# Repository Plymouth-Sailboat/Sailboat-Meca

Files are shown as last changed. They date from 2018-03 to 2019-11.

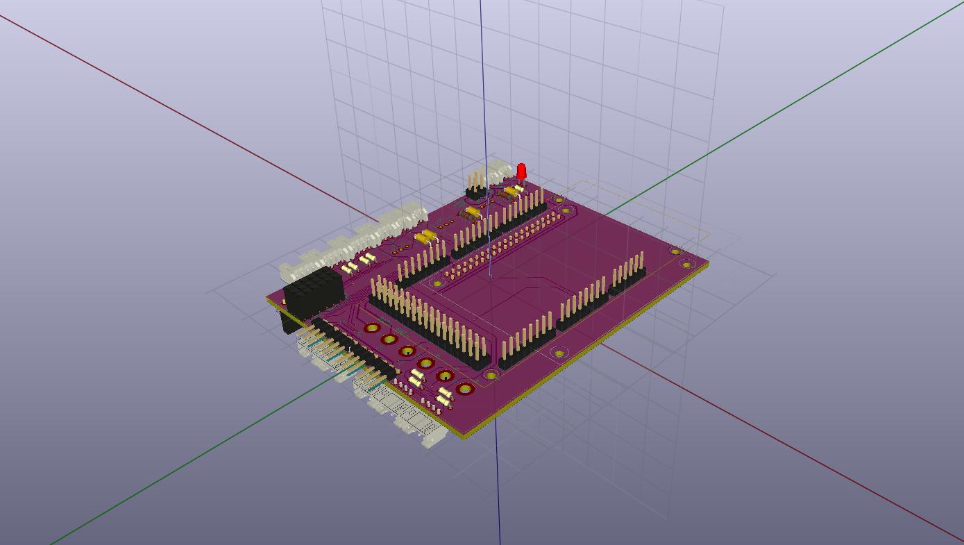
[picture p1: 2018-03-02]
Electronic Board/SailboatMainBoard.jpg

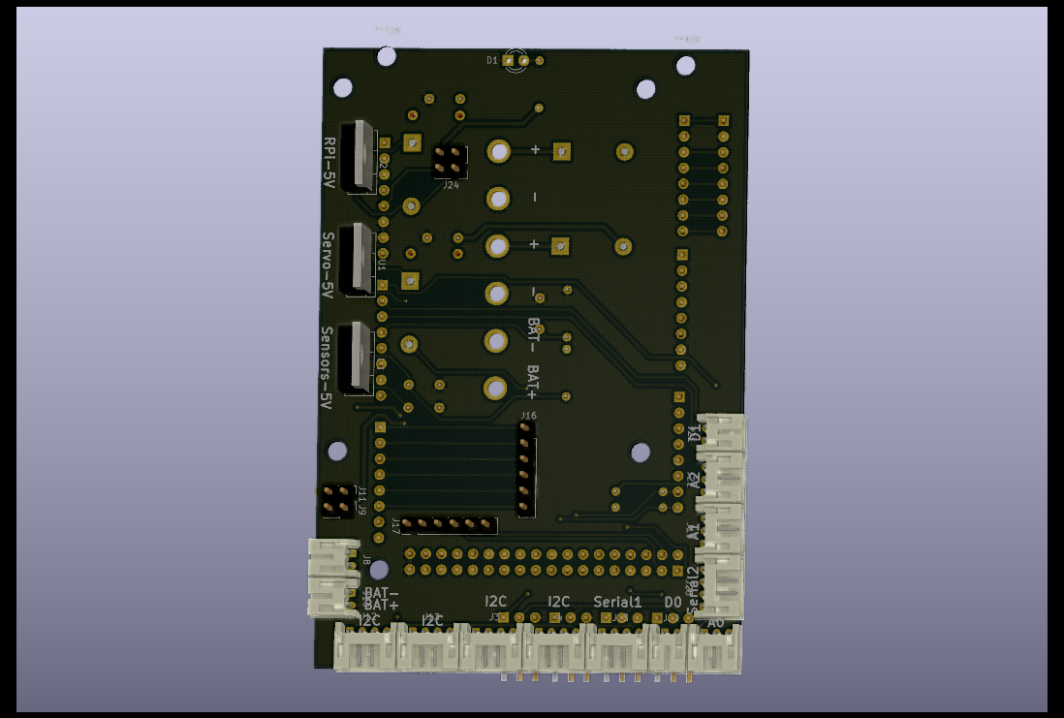
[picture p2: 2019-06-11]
Electronic Board/Sailboat Kicad/Board1-Arduino/3D/ArduinoIntBack.png

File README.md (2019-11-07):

# Sailboat-Meca

boatgif

This repository lists all the mechanical documents of the sailboat - Electronic Board and 3D Parts. It is used in conjunction with the [Arduino Repository](https://github.com/Plymouth-Sailboat/SailBoatArduinoInterface) and the [Raspberry Pi Repository](https://github.com/Plymouth-Sailboat/SailBoatROS).
This project was done by [Ulysse Vautier](https://ulyssevautier.github.io/) for his PhD in Autonomous Sailboat Navigation System at the University of Plymouth.

**A complete tutorial is available on the** [wiki](https://github.com/Plymouth-Sailboat/Sailboat-Meca/wiki).

The goal of such a project is to make an affordable, accessible and expandable control box to transform a RC sailboat into an autonomous Sailboat easily. The control box costs £86 to make.  
Once connected to the different sensors and actuators of the sailboat, it transforms it into an autonomous sailboat with already implemented navigation algorithms. Please see the [list of control algorithms](https://github.com/Plymouth-Sailboat/SailBoatROS/wiki/Controllers-List) already implemented.

Another option is to use off-the-shelf Shields to act as a connector interface for the Arduino. This is a cheaper alternative to the custom board, but removes the compactness of it. This is explained in the [wiki](https://github.com/Plymouth-Sailboat/Sailboat-Meca/wiki).

**For more information look at the Wikis. The project is separated into 3 categories : [SailboatMeca](https://github.com/Plymouth-Sailboat/Sailboat-Meca), [SailBoatROS](https://github.com/Plymouth-Sailboat/SailBoatROS) and [SailboatArduinoInterface](https://github.com/Plymouth-Sailboat/SailBoatArduinoInterface).**

**[SailboatMeca](https://github.com/Plymouth-Sailboat/Sailboat-Meca) explains the hardware configuration of the boat. The sensors that are used, how to build the control box and how to attach all the components to the control box.**

**[SailBoatROS](https://github.com/Plymouth-Sailboat/SailBoatROS) contains the code on the Raspberry Pi. It explains how to have a full environment ready on the Raspberry Pi 3B and Raspberry Pi 3B+ to have a working boat.**

**[SailBoatArduinoInterface](https://github.com/Plymouth-Sailboat/SailBoatArduinoInterface) explains how to upload the code to the Arduino. It also explains how to change the configuration files or how to add sensors to comply with your hardware configuration.  
Please look at all their wikis and READMEs.**

# Structure of this Repository

You fill find the 3D prints for waterproofing our sensors and the complete KiCad project for our Custom Circuit Board. The KiCad projects come with 3D models of the boards and the Gerber files needed to manufacture them.

# Off-The-Shelf System

Assembled System

This is a new hardware architecture using mostly commercial modules for Arduino and Raspberry Pi, using [SeeedStudio grove shields](http://wiki.seeedstudio.com/Grove_System/). This version is a bit bigger but a cheaper and more easily attainable than manufactured custom boards.  
All the previous components used are still compatible, only connectors need to be changed. Also the battery used are Li-ion battery packs now. Everything is explained in the [wiki](https://github.com/Plymouth-Sailboat/Sailboat-Meca/wiki).

# Custom Circuit Board

Arduino Interface Board

Our custom board is composed of two boards, stacking with each others. One stacking with the Arduino Mega and another one stacking with the Raspberry Pi.
These custom boards manages power, connection to sensors and motors and communications between Raspberry Pi, the Arduino and all the peripheral devices.

## Arduino Interface Board

The Arduino Interface Board exports the Arduino's connector to interface them with strong, more robust JST connectors. This board also manages the power to all of the peripheral devices. You can find the complete KiCad Project, Gerber files and 3Ds of the boards at [Arduino Interface Board Folder](/Electronic%20Board/Sailboat%20Kicad/Board1-Arduino).  
This board stacks with the Arduio Mega and the Raspberry Pi Interface Board below.

## Raspberry Pi Interface Board

The Raspberry Pi Board is only a board to level all the components to make the overall structure compact. It connects the power to the Raspberry Pi and interface the Radio Receiver to the Arduino. You can find the complete KiCad Project, Gerber files and 3Ds of the boards at [Raspberry Pi Interface Board Folder](/Electronic%20Board/Sailboat%20Kicad/Board2-RPI).   
This board stacks with the Arduino Interface Board and the Raspberry Pi.

# Bill Of Material

The bill of material is available [here](BOM.xlsx). It details all the mechanical and electrical components with the sensors and motors for our boats. It also gives all the link to suppliers to buy the components we use. We mainly purchase our components from [RS](https://uk.rs-online.com/web/) and we use a third-party manufacturer to make the boards [SeeedStudio](https://www.seeedstudio.com/fusion_pcb.html).

The overall price of a whole autonomous sailboat comes to £605.65 (considering the IMU used is 1/3 of the price). The custom board itself costs £86 overall - with third-party service to print the boards.

# Installation

## Requirements

* Raspberry Pi 3 Model B with [ROS and our package](https://github.com/Plymouth-Sailboat/SailBoatROS)
* Arduino Mega with [our code](https://github.com/Plymouth-Sailboat/SailBoatArduinoInterface)
* Custom Boards above

All the installation for each of these devices are explained in their respective Repository.

To get your custom board printed via SeeedStudio, we suggest following the tutorial in the [wiki](https://github.com/Plymouth-Sailboat/Sailboat-Meca/wiki)

Once the boards are soldered all you need is to stack them with the Arduino and Raspberry Pi. Connect your Raspberry Pi to the Arduino via USB and your Control Box is ready to host a new sailboat.

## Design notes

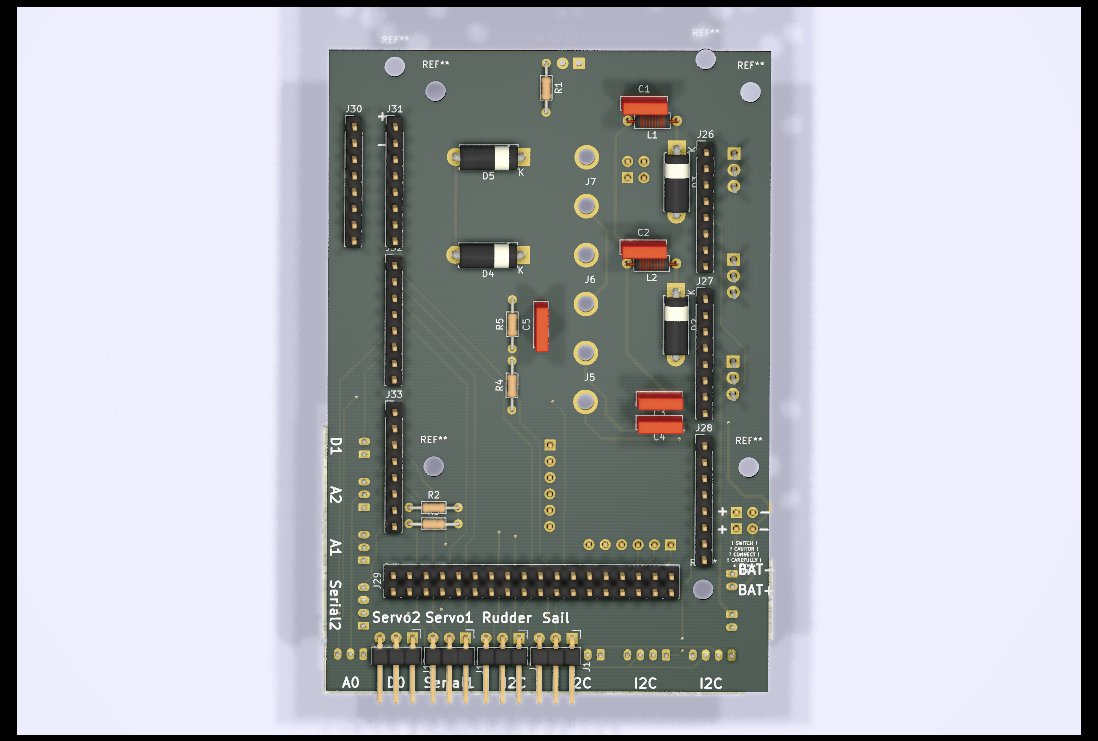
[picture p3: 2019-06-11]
Electronic Board/Sailboat Kicad/Board1-Arduino/3D/ArduinoIntFront.png

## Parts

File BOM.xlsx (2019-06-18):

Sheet: BOM
Name | Description | Price | Source
Boat | Rubix
PCB Boards |  | £80.51 | Card Component'!A1
SeeedStudio | PCB Manufacturing x 2 | £6.00 | https://www.seeedstudio.com/fusion_pcb.html
Mechanical Parts |  | £32.82 | Mechanical Parts'!A1
Sensors |  | £434.36 | Sensors!A1
Battery | 2S 4000mAh | £12.44 | https://hobbyking.com/en_us/turnigy-4000mah-2s-30c-hardcase-pack-roar-approved-de-warehouse.html
Raspberry Pi 3 B |  | £32.00 | https://thepihut.com/products/raspberry-pi-3-model-b
Arduino Mega |  | £7.53 | https://hobbyking.com/en_us/mega-2560-r3-atmega2560-16au-board-plus-usb-cable-1.html
 |  | £605.65 | Note that most of the cost comes from the sensors. Cheaper alternatives can be found for the sensors and it will still be compatible with the whole system.

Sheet: Card Component
Name | Value | Quantity | Reference | Description | Price exc VAT | Price | Total | Source | VAT | 1.2
Capacitor | 0.33uF | 1 | C320C334M5U5TA |  | £0.11 | 0.1332 | £0.11 | https://uk.rs-online.com/web/p/ceramic-multilayer-capacitors/8015390/
Capacitor | 0.1uF | 1 | C315C104M5U5TA |  | £0.08 | 0.0912 | £0.08 | https://uk.rs-online.com/web/p/ceramic-multilayer-capacitors/5381203/
Capacitor | 4.7uF | 2 | C320C475K3N5TA91707301 |  | £0.29 | 0.3504 | £0.58 | https://uk.rs-online.com/web/p/ceramic-multilayer-capacitors/1365581/
Inductor | 3.3uH | 2 | B78108S1332K000 |  | £0.29 | 0.3468 | £0.58 | https://uk.rs-online.com/web/p/leaded-inductors/1910431/
JST-PH-S2B Angled |  | 3 | S2B-PH-K-S |  | £0.38 | 0.456 | £1.14 | https://uk.rs-online.com/web/p/pcb-headers/8201494
JST-PH-S3B Angled |  | 3 | S3B-PH-K-S |  | £0.38 | 0.456 | £1.14 | https://uk.rs-online.com/web/p/pcb-headers/8201504
JST-PH-S4B Angled |  | 2 | S4B-PH-K-S |  | £0.38 | £0.46 | £0.76 | https://uk.rs-online.com/web/p/pcb-headers/8201507/
LED | G | 1 |  |  |  | £0.00 | £0.00
Pin Header 1x2 |  | 2 | 251-8086 |  | £0.08 | £0.10 | £0.16 | https://uk.rs-online.com/web/p/pcb-headers/2518086/
Pin Header 1x3 Angled |  | 3 | 90121-0763 |  | £0.43 | £0.52 | £1.30 | https://uk.rs-online.com/web/p/pcb-headers/3606437/
Pin Header 1x6 |  | 2 | 68000-406HLF |  | £0.20 | £0.24 | £0.40 | https://uk.rs-online.com/web/p/pcb-headers/6812994/
Pin Header 1x8 |  | 6 | M20-9990846 |  | £0.20 | £0.24 | £1.20 | https://uk.rs-online.com/web/p/pcb-headers/6812991/
Pin Header 2x18 |  | 0 | 90131-0138 |  | £0.84 | £1.01 | £0.00 | https://uk.rs-online.com/web/p/pcb-headers/6703487/
Pin Header 2x2 |  | 1 | 826632-2 |  | £0.28 | £0.33 | £0.28 | https://uk.rs-online.com/web/p/pcb-headers/6695288/
Regulator | L7805 | 1 | L7805CV | 5V 1.5A | £0.59 | £0.71 | £0.59 | https://uk.rs-online.com/web/p/linear-voltage-regulators/7931346/
Regulator | R-78B5.0-2.0 | 2 | R-78B5.0-2.0 | 5V 2A | £7.94 | £9.53 | £15.88 | https://uk.rs-online.com/web/p/switching-regulators/1392959/
Resistor | 330 | 1 | LR1F330R |  | £0.05 | £0.06 | £0.05 | https://uk.rs-online.com/web/p/through-hole-fixed-resistors/0148382/
Resistor | 4k7 | 2 | 707-7726 |  | £0.10 | £0.12 | £0.20 | https://uk.rs-online.com/web/p/through-hole-fixed-resistors/7077726/
Socket Header 1x3 |  | 7 | 251-8187 |  | £0.32 | £0.38 | £2.22 | https://uk.rs-online.com/web/p/pcb-sockets/2518187/
Socket Header 1x6 |  | 2 | 4320-01074-0 |  | £0.94 | £1.12 | £1.87 | https://uk.rs-online.com/web/p/pcb-sockets/1613692/
Socket Header 1x8 |  | 1 | 215297-8 |  | £0.69 | £0.83 | £0.69 | https://uk.rs-online.com/web/p/pcb-sockets/4958587/
Socket Header 2x2 |  | 1 | 803-87-004-10-001101 |  | £0.45 | £0.54 | £0.45 | https://uk.rs-online.com/web/p/pcb-sockets/7022934/
Socket Header 2x20 |  | 1 | A-BL254-DG-G40D |  | £1.78 | £2.13 | £1.78 | https://uk.rs-online.com/web/p/pcb-sockets/6742369/
Schottky Diode |  | 4 | SR560 |  | £0.07 | £0.09 | £0.30 | https://uk.rs-online.com/web/p/rectifier-schottky-diodes/9179120/
Resistor | 20k | 1 | LR1F20K |  | £0.04 | £0.05 | £0.04 | https://uk.rs-online.com/web/p/through-hole-fixed-resistors/1251166/
Resistor | 12k | 1 | MRS25000C1202FCT00 |  | £0.08 | £0.09 | £0.08 | https://uk.rs-online.com/web/p/through-hole-fixed-resistors/6832989/
RMG Switch |  | 1 |  |  | £34.50 | £41.40 | £34.50 | https://www.rmgsailwinch.com.au/rmg/products/RMGSwitch%252dStd.html
HXT 4 Prebuilt |  | 1 |  |  | £0.72 | £0.86 | £0.72 | https://hobbyking.com/en_us/hxt-4mm-gold-connector-w-pre-installed-bullets-10pcs-set.html
 |  |  |  |  |  |  | £67.09
 |  |  |  |  |  |  | £80.51

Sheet: Mechanical Parts
Name | Value | Quantity | Reference | Description | Price exc VAT | Price | Total | Source | VAT | 1.2
RMG Sailwinch |  | 1 |  | Excluded in total | £206.60 | £247.92 | £206.60 | https://www.rmgsailwinch.com.au/rmg/products/380ES.html
KingMax Servo |  | 1 |  |  | £24.99 | £29.99 | £24.99 | https://www.componentshop.co.uk/61g-digital-sail-winch-servo-6-turn-programmable.html
Threaded Inserts M3 |  | 20 |  |  | £0.10 | £0.12 | £1.92 | https://uk.rs-online.com/web/p/inserts/0278534/
Spacers | 10mm | 10 | R30-3001002 |  | £0.01 | £0.01 | £0.07 | https://uk.rs-online.com/web/p/threaded-hex-spacers/1256002/
HXT4mm Cable |  | 1 |  |  | £0.76 | £0.92 | £0.76 | https://hobbyking.com/en_us/hxt4mm-w-12awg-silicon-wire-10cm-esc-side-5pcs-bag.html
Flex Ribbon Rpi | 300mm | 1 |  |  | £2.00 | £2.40 | £2.00 | https://thepihut.com/products/adafruit-flex-cable-for-raspberry-pi-camera-300mm-12
Velcro | 1m | 1 |  |  | £3.07 | £3.68 | £3.07 | https://hobbyking.com/en_us/polyester-velcro-peel-n-stick-self-adhesive-v-strong-1mtr.html
 |  |  |  |  |  | £0.00 | £0.00
 |  |  |  |  |  |  | £32.82
 |  |  |  |  |  |  | £39.38
 |  |  |  |  |  | Big Boat | £214.43

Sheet: Sensors
Name | Value | Quantity | Reference | Description | Price exc VAT | Price | Total | Source | VAT | 1.2
Xsens |  | 1 | Mti-3-8A7G6-DK | AHRS+Compass | £262.78 | £315.34 | £262.78 | https://shop.xsens.com/shop/mti-1-series/mti-1-series-dk/mti-3-8a7g6-dk
GPS Module |  | 1 |  |  | £5.08 | £6.10 | £5.08 | https://www.banggood.com/GPS-Module-with-Ceramic-Antenna-GPS-Receiver-TTL9600-Ublox-Module-for-Multirotor-p-1100984.html
Radio Transmitter + Receiver 6CH |  | 1 | T6A |  | £14.27 | £17.12 | £14.27 | https://hobbyking.com/en_us/hobby-king-2-4ghz-6ch-tx-rx-v2-mode-1.html
Wind Sensor |  | 1 | e-vane |  | £91.50 | £109.80 | £91.50 | https://www.inspeed.com/wind_speed_direction/Vane.asp
Raspberry Pi Camera |  | 1 |  |  | £24.50 | £29.40 | £24.50 | https://www.modmypi.com/pis-and-peripherals-1139/raspberry-pi-camera-board-v2-8mp1080p
AIS Receiver |  | 1 | B01GDN1T4S |  | £28.98 | £34.78 | £28.98 | https://www.amazon.co.uk/NooElec-NESDR-SMArt-Enclosure-R820T2-Based/dp/B01GDN1T4S
JST PHR-2 |  | 3 | PHR-2 |  | £0.03 | £0.04 | £0.09 | https://uk.rs-online.com/web/p/pcb-connector-housings/8201466/
JST PHR-3 |  | 2 | PHR-3 |  | £0.04 | £0.04 | £0.07 | https://uk.rs-online.com/web/p/pcb-connector-housings/8201475/
JST PHR-4 |  | 2 | PHR-4 |  | £0.04 | £0.05 | £0.08 | https://uk.rs-online.com/web/p/pcb-connector-housings/8201478/
JST Cable |  | 15 | SPH-26L-300 |  | £0.47 | £0.56 | £7.01 | https://uk.rs-online.com/web/p/products/8201412/
 |  |  |  |  |  | £0.00 | £0.00
 |  |  |  |  |  |  | £434.36
 |  |  |  |  |  |  | £521.23

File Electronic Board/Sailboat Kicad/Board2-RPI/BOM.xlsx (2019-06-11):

Id | Designator | Package | Quantity | Designation | Supplier and ref
1 | J29,J25,J26,J27,J28,J30,J4 | Socket_Strip_Straight_1x03_Pitch2.54mm | 7 | Conn_01x03_Female
2 | J33 | Socket_Strip_Straight_1x08_Pitch2.54mm | 1 | Conn_01x08_Female
3 | J23,J5 | Pin_Header_Straight_2x20_Pitch2.54mm | 2 | Conn_02x20_Odd_Even
4 | J1,J2 | Socket_Strip_Straight_1x06_Pitch2.54mm | 2 | Conn_01x06
5 | J3 | Socket_Strip_Straight_2x02_Pitch2.54mm | 1 | Conn_02x02_Odd_Even
6 | REF**,REF**,REF**,REF**,REF**,REF** | MountingHole_3.2mm_M3 | 6 | MountingHole_3.2mm_M3

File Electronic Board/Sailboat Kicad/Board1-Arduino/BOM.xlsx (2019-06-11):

Id | Designator | Package | Quantity | Designation | Supplier and ref
1 | J20,J8,J10,J21 | JST_PH_S2B-PH-K_1x02_P2.00mm_Horizontal | 4 | Conn_01x02_Male
2 | D1 | LED_D3.0mm | 1 | G
3 | REF**,REF**,REF**,REF**,REF**,REF**,REF** | MountingHole_3.2mm_M3 | 7 | MountingHole_3.2mm_M3
4 | J28,J30,J32,J27,J31,J33,J26 | PinHeader_1x08_P2.54mm_Vertical | 7 | Conn_01x08_Male
5 | J29 | PinHeader_2x18_P2.54mm_Vertical | 1 | Conn_02x18_Odd_Even
6 | J4,J3,J13,J23,J25,J12 | JST_PH_S4B-PH-K_1x04_P2.00mm_Horizontal | 6 | Conn_01x04_Male
7 | J5,J7,J6 | BAT-CONN | 3 | Conn_01x02_Female
8 | J18,J19,J22 | JST_PH_S3B-PH-K_1x03_P2.00mm_Horizontal | 3 | Conn_01x03_Male
9 | J1,J15,J14,J2 | PinHeader_1x03_P2.54mm_Horizontal | 4 | Conn_01x03_Male
10 | J11,J9 | PinHeader_1x02_P2.54mm_Vertical | 2 | Conn_01x02_Male
11 | J24 | PinHeader_2x02_P2.54mm_Vertical | 1 | Conn_02x02_Odd_Even
12 | J16,J17 | PinHeader_1x06_P2.54mm_Vertical | 2 | Conn_01x06_Male
13 | R5 | R_Axial_DIN0204_L3.6mm_D1.6mm_P7.62mm_Horizontal | 1 | 12k
14 | R2,R3 | R_Axial_DIN0204_L3.6mm_D1.6mm_P7.62mm_Horizontal | 2 | 4k7
15 | R4 | R_Axial_DIN0204_L3.6mm_D1.6mm_P7.62mm_Horizontal | 1 | 20k
16 | U3,U1,U2 | TO-220-3_Vertical | 3 | L7805
17 | L1,L2 | L_Axial_L5.3mm_D2.2mm_P7.62mm_Horizontal_Vishay_IM-1 | 2 | 3.3uH
18 | C1,C2 | C_Rect_L7.0mm_W2.0mm_P5.00mm | 2 | 4.7uF
19 | R1 | R_Axial_DIN0204_L3.6mm_D1.6mm_P7.62mm_Horizontal | 1 | 330
20 | D4,D5,D2,D3 | D_5W_P10.16mm_Horizontal | 4 | D_Schottky
21 | C3 | C_Rect_L7.0mm_W2.0mm_P5.00mm | 1 | 0.33uF
22 | C4 | C_Rect_L7.0mm_W2.0mm_P5.00mm | 1 | 0.1uF
23 | C5 | C_Rect_L7.0mm_W2.0mm_P5.00mm | 1 | 1uF

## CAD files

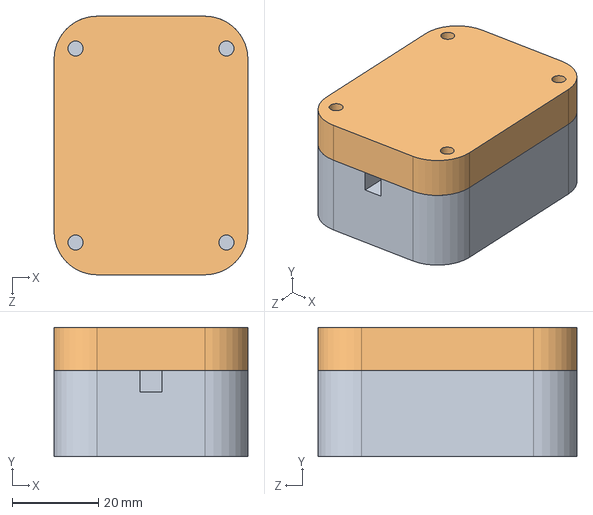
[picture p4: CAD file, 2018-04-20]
3D Prints/Adafruit Ultimate GPS Box/GPS.SLDASM
45.0 x 30.0 x 60.0 mm
GPSBot
GPSTop

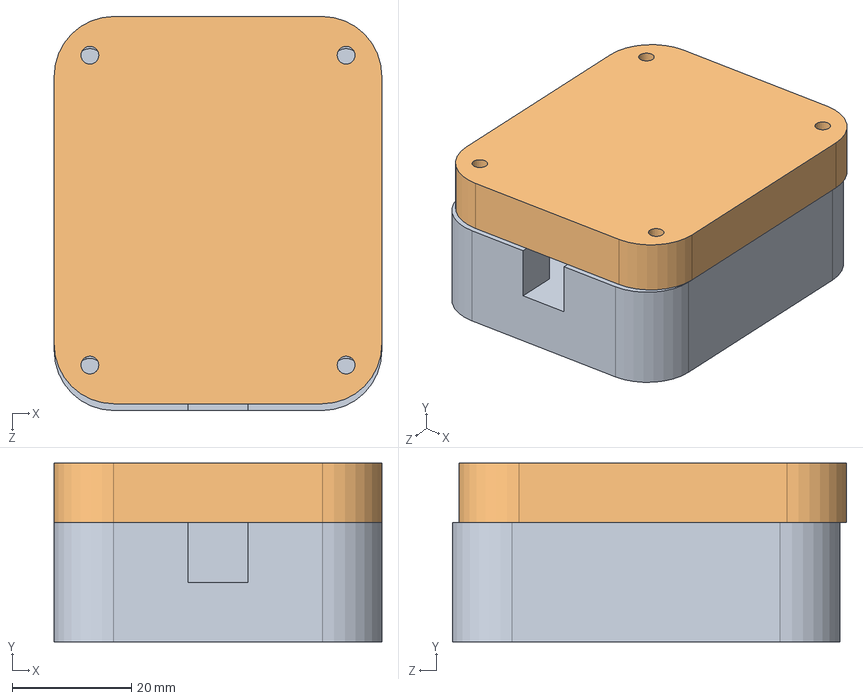
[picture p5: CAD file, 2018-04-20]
3D Prints/XSens Box/Xsens.SLDASM
55.0 x 30.0 x 66.1 mm
XSensBot
XSensTop

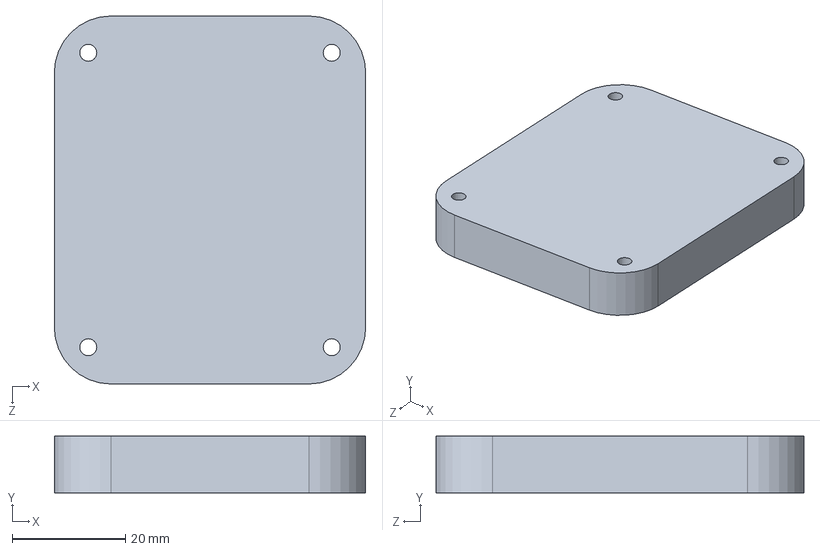
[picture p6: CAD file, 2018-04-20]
3D Prints/XSens Box/XSensTop.SLDPRT
55.0 x 10.0 x 65.0 mm

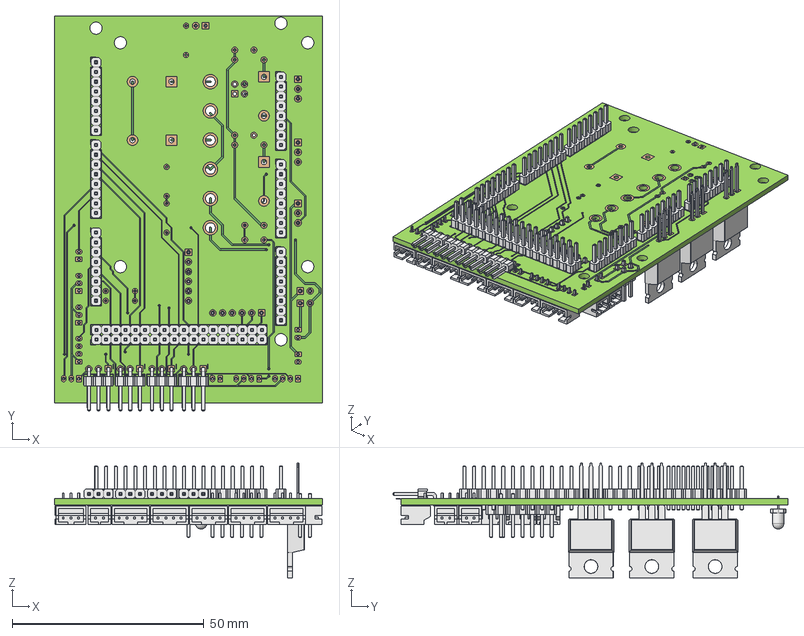
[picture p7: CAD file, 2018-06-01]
Electronic Board/Sailboat Kicad/Board1-Arduino/3D/ArduinoInt.FCStd
70.0 x 103.1 x 30.0 mm
Board
D1
J11
J12
J13
J14
J15
J16
J17
J18
J19
J20
J21
J22
J24
J31
J32
J3
J4
J5
J6
J7
J8
U1
U2
U3
J34
J35
J36
J37
J2
J23
J25
F_Cu_0
bPad_107
tPad_108
B_Cu_31
B_SilkS_36
F_SilkS_37

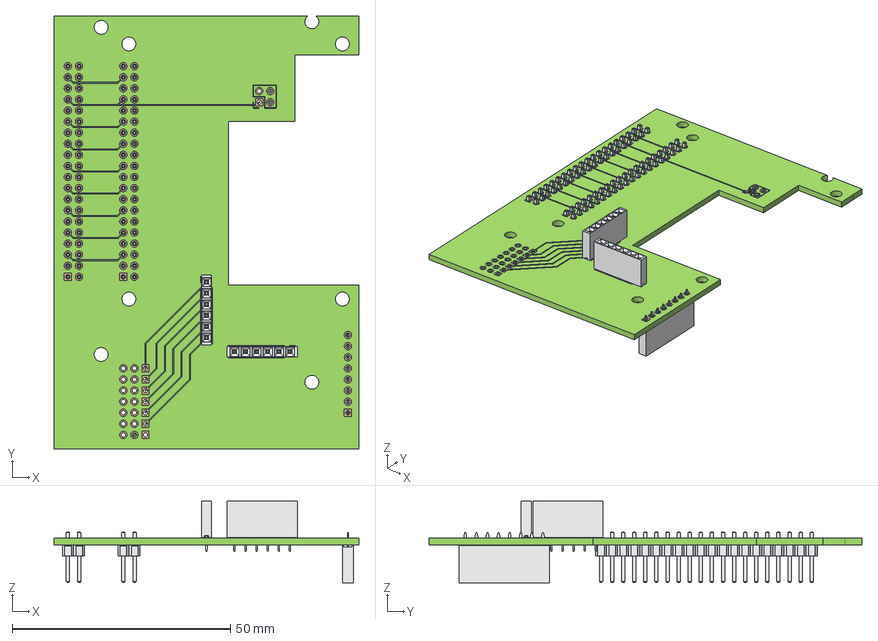
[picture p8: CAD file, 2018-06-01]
Electronic Board/Sailboat Kicad/Board2-RPI/3D/RPiInt.FCStd
69.9 x 99.1 x 18.7 mm
Board
J33
J23
J1
J2
J5
F_Cu_0
bPad_107
tPad_108
B_Cu_31
B_SilkS_36
F_SilkS_37

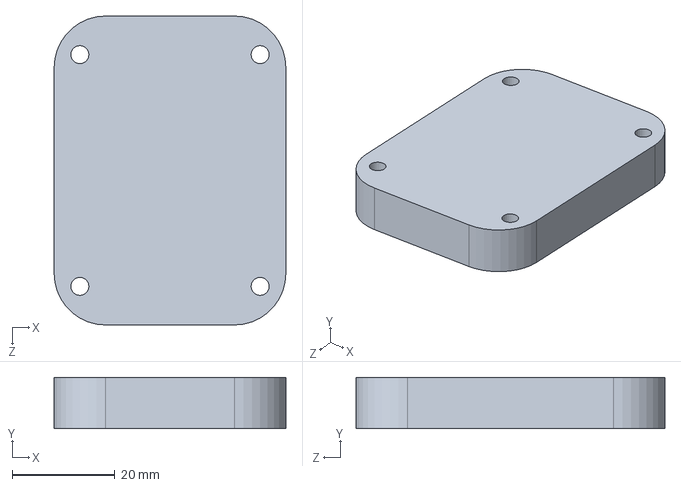
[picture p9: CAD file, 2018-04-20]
3D Prints/Adafruit Ultimate GPS Box/GPSTop.SLDPRT
45.0 x 10.0 x 60.0 mm

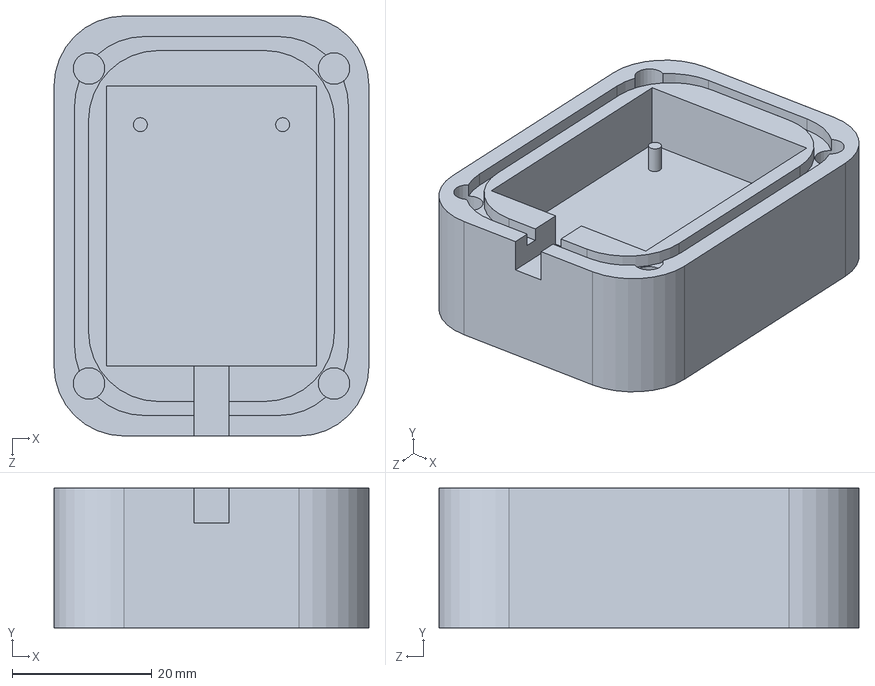
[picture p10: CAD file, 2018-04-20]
3D Prints/Adafruit Ultimate GPS Box/GPSBot.SLDPRT
45.0 x 20.0 x 60.0 mm

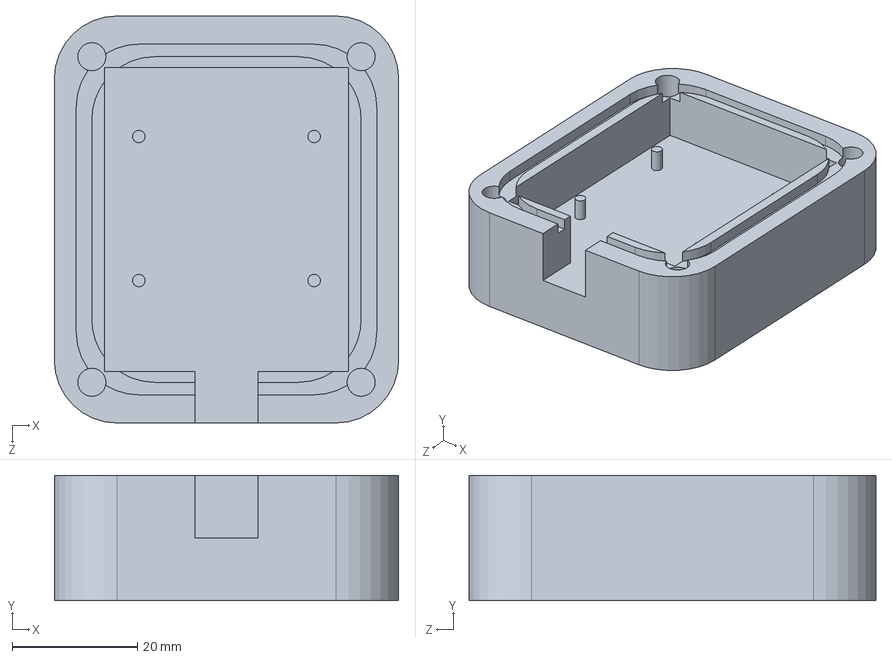
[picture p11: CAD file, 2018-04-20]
3D Prints/XSens Box/XSensBot.SLDPRT
55.0 x 20.0 x 65.0 mm

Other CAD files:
3D Prints/Adafruit Ultimate GPS Box/GPSBot.STL
3D Prints/Adafruit Ultimate GPS Box/GPSTop.STL
3D Prints/XSens Box/XSensBot.STL
3D Prints/XSens Box/XSensTop.STL
Electronic Board/Sailboat Kicad/Board2-RPI/3D/RPiInt.stl

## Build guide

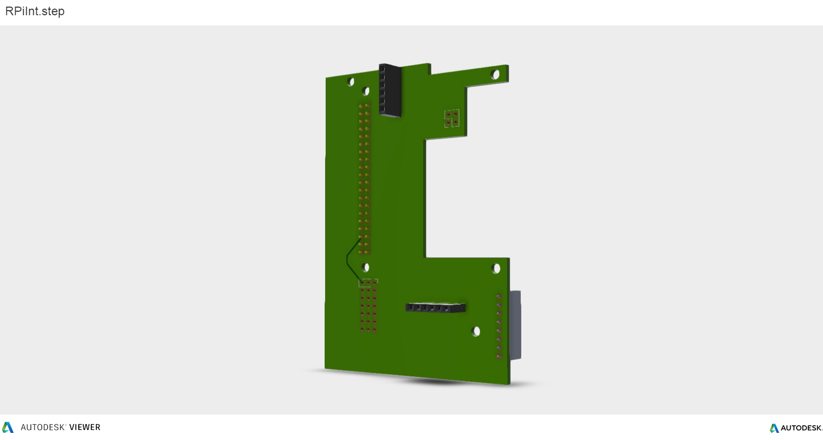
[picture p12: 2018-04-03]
Electronic Board/Sailboat Kicad/Board2-RPI/3D/RPiInt.step.png

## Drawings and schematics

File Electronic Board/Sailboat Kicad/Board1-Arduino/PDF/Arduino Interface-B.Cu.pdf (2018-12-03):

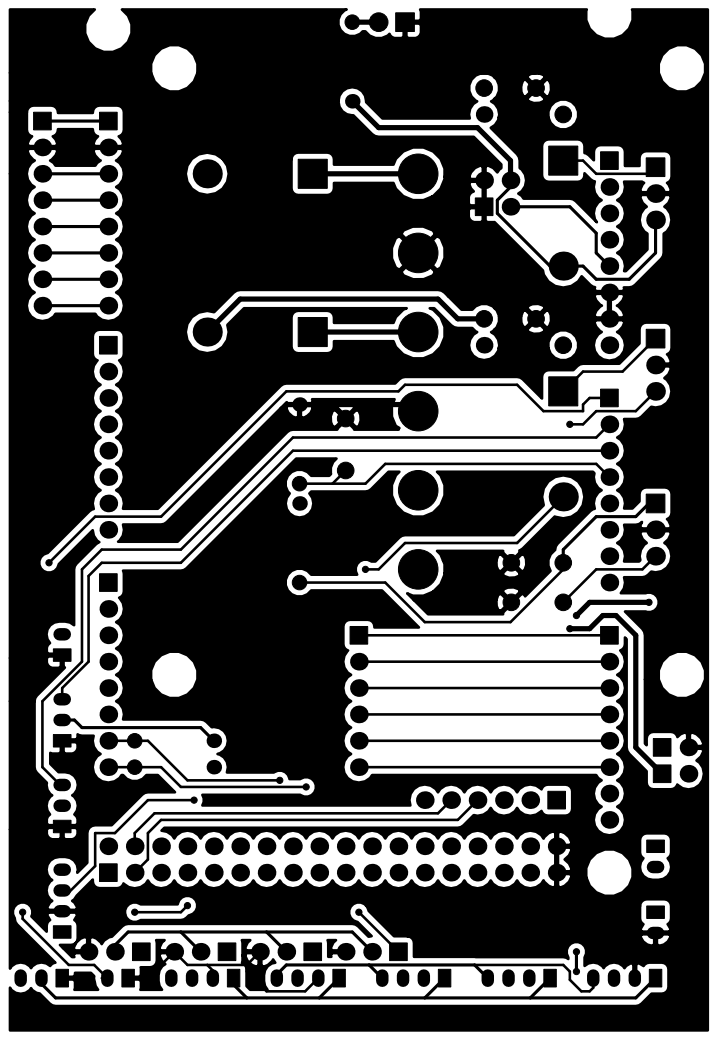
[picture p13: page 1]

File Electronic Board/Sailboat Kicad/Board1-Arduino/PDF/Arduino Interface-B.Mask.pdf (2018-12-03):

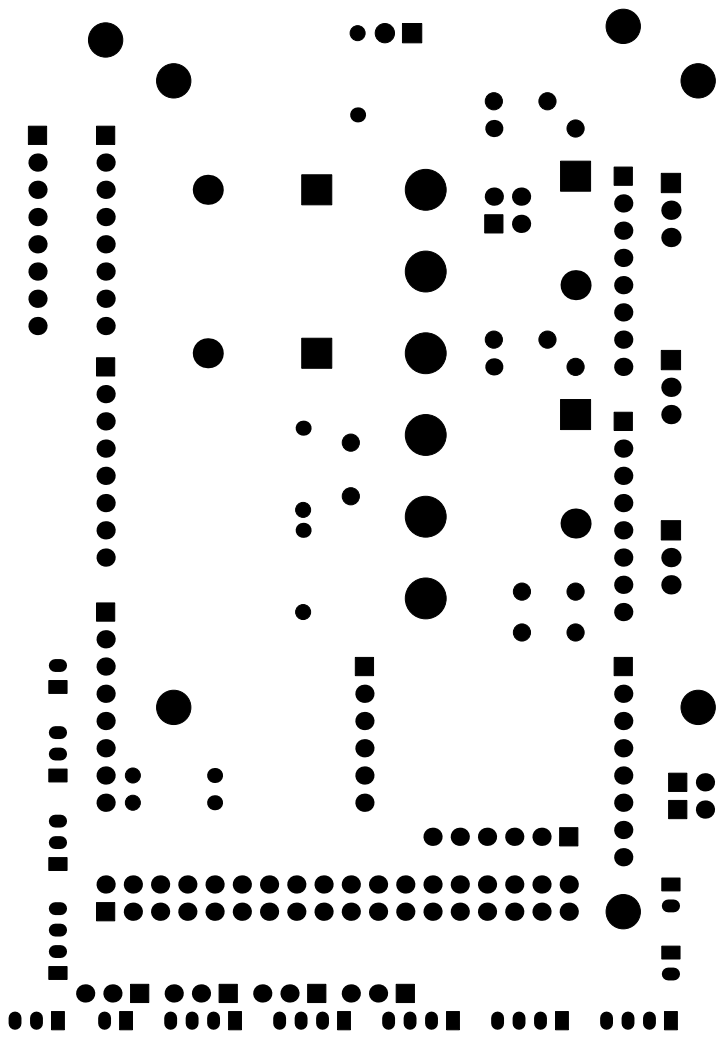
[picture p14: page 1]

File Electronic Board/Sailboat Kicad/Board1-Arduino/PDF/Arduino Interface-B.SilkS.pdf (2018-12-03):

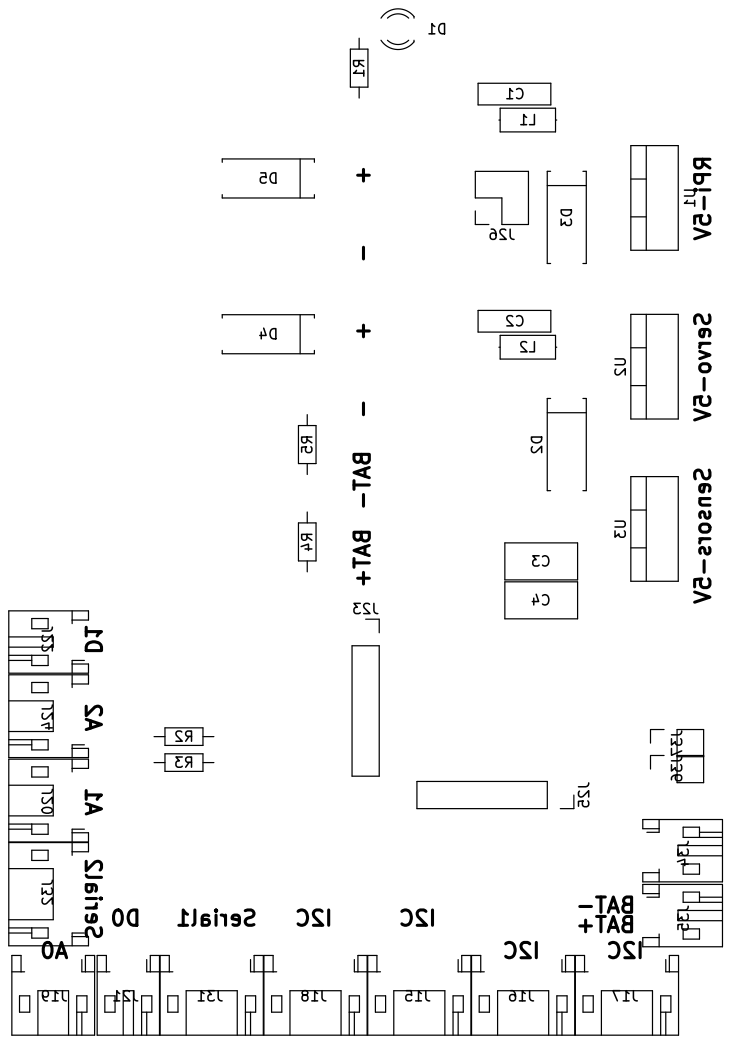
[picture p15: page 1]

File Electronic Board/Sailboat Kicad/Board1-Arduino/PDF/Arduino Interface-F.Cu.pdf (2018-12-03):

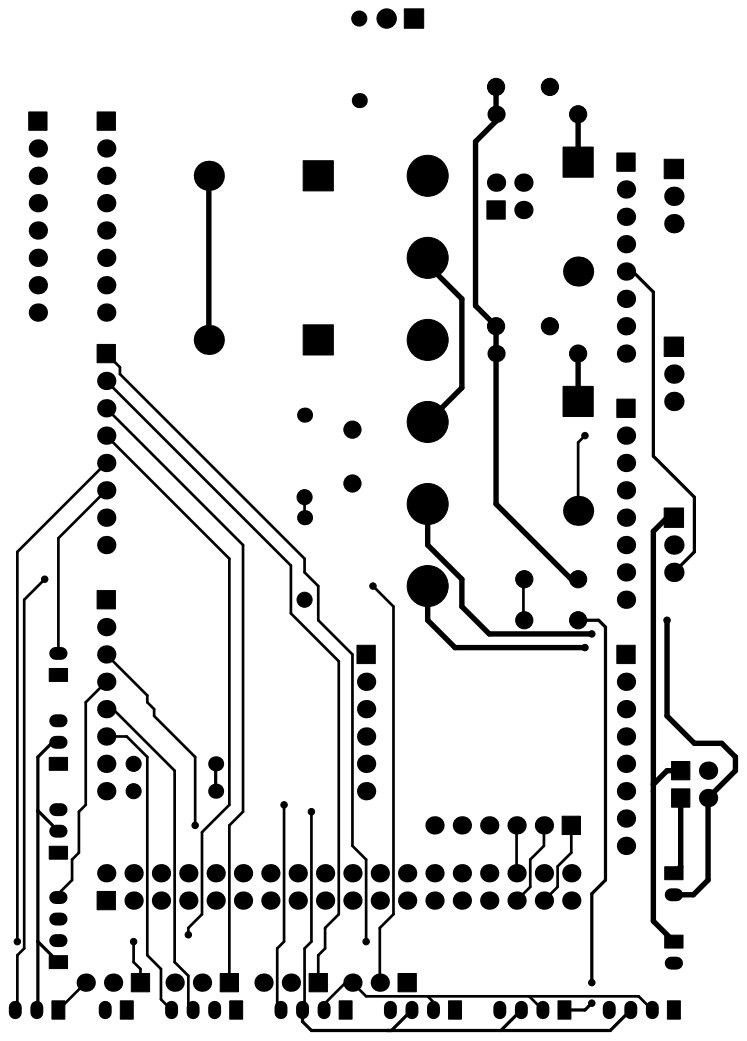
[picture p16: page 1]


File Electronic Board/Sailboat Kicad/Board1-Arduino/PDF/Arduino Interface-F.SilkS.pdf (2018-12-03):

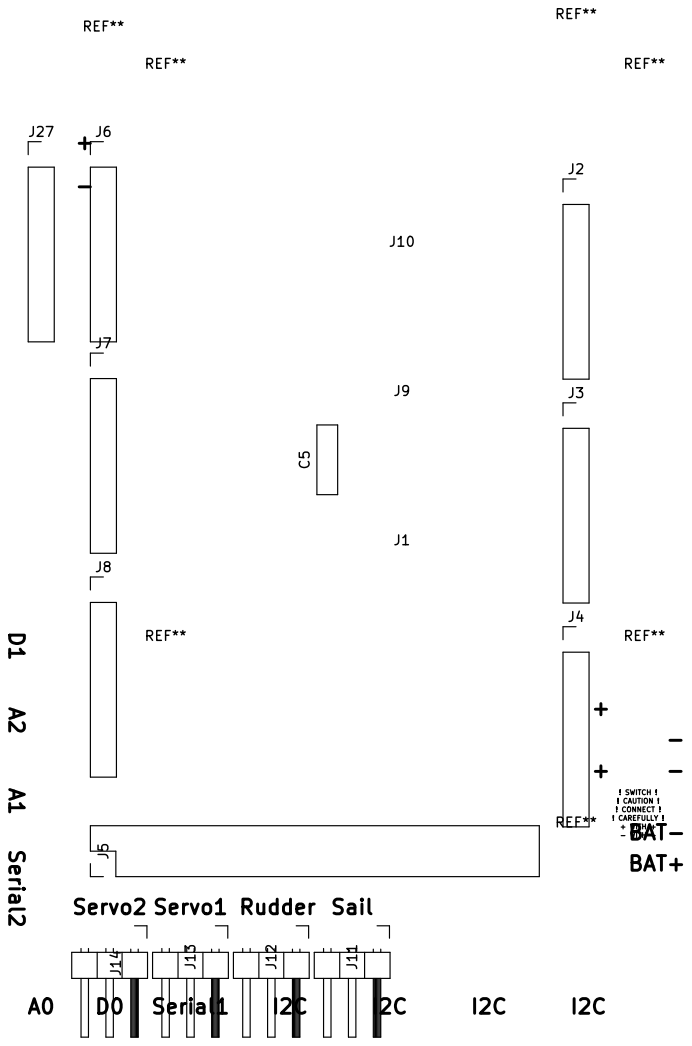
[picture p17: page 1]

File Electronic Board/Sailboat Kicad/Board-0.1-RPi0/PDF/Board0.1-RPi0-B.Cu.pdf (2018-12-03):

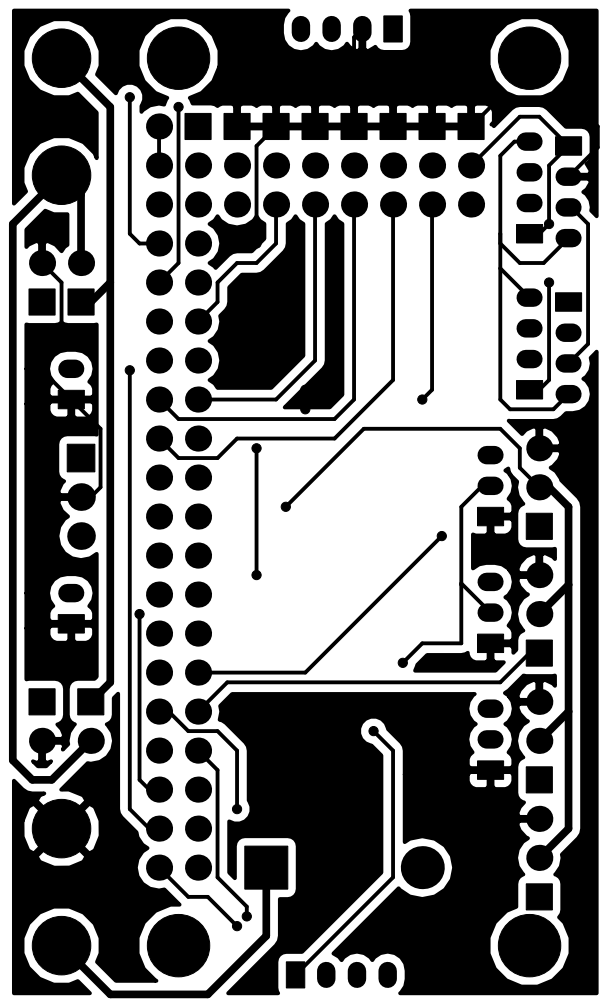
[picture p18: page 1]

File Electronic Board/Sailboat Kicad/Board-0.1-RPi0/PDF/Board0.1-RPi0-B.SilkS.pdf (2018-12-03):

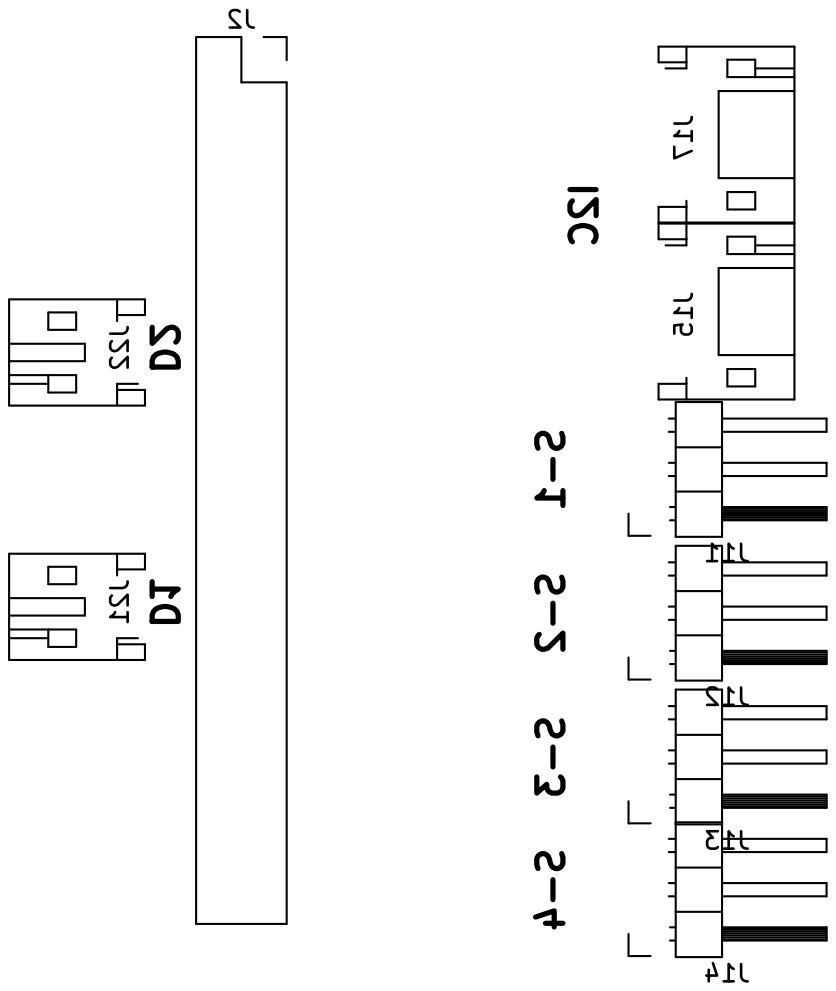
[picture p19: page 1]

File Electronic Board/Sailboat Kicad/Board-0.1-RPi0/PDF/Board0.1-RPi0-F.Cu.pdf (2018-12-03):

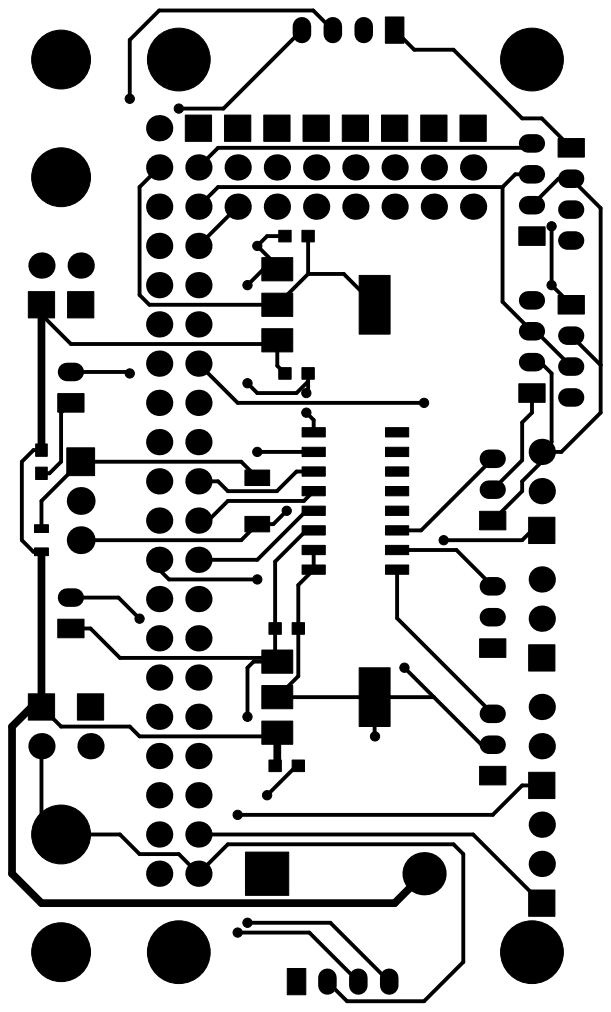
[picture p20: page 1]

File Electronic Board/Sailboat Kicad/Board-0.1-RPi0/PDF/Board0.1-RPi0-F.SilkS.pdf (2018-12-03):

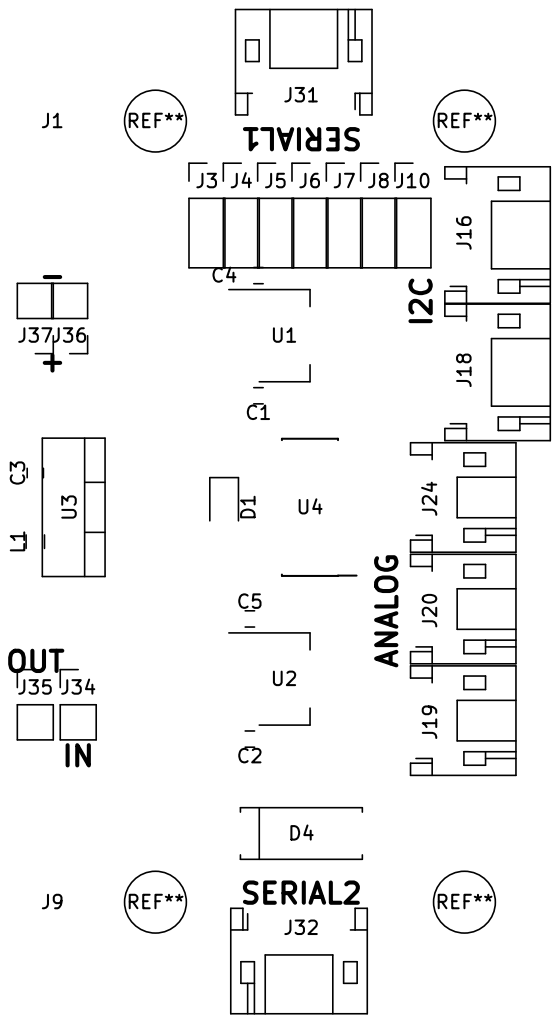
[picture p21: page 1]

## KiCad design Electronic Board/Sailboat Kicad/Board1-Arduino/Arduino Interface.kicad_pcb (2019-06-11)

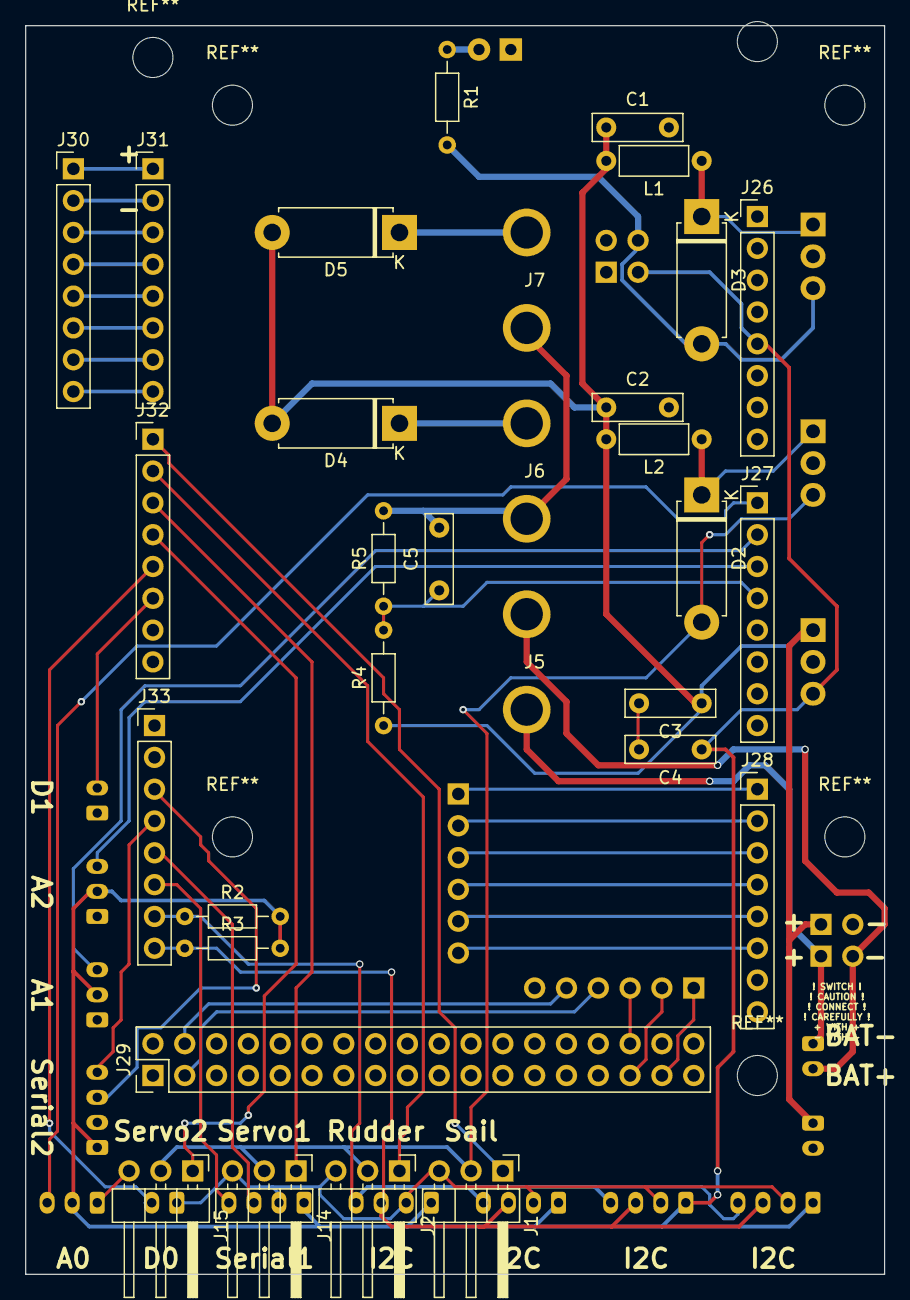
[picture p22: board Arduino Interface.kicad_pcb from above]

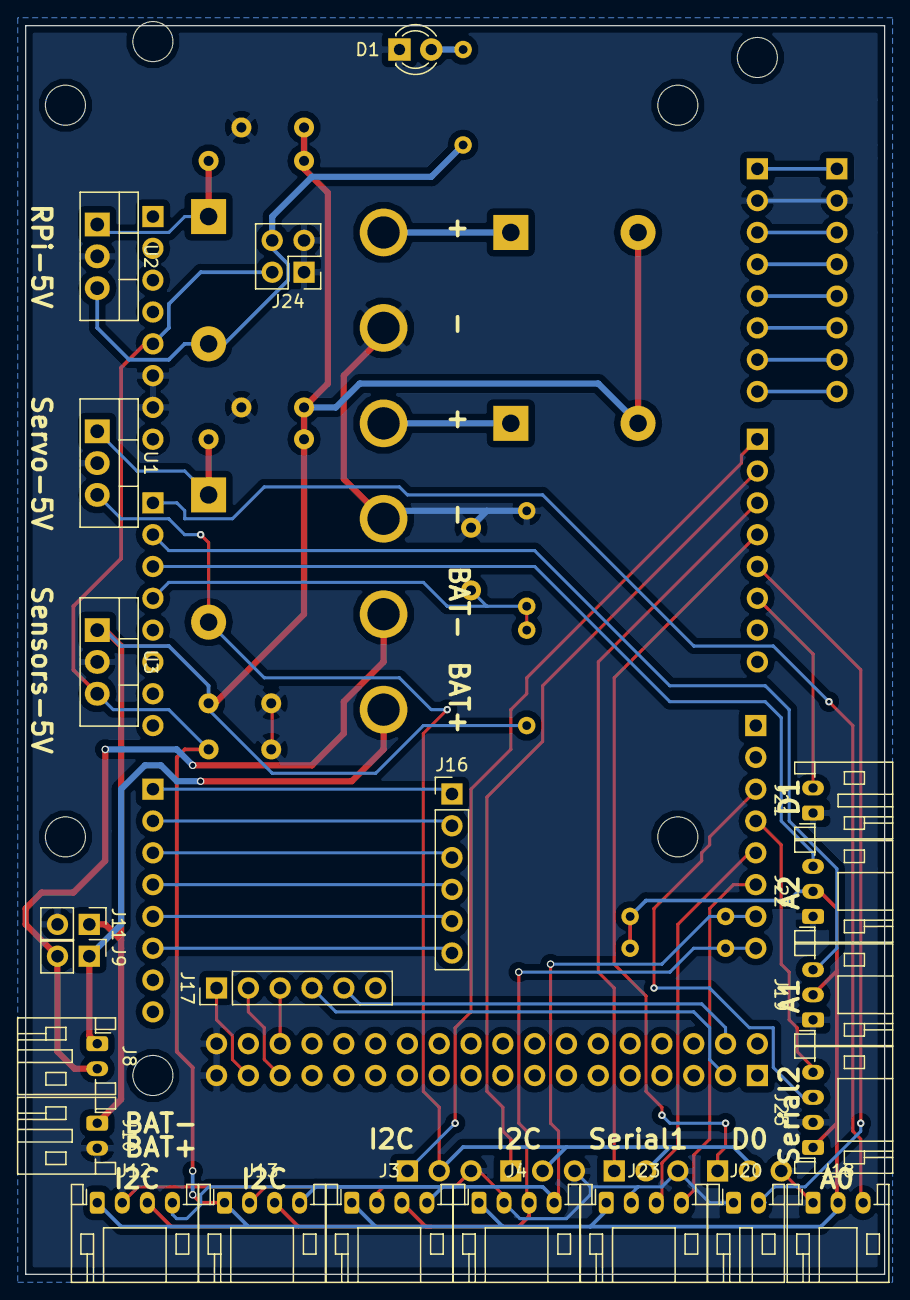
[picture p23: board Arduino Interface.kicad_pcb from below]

Board: 2 copper layers, 68.6 x 99.7 mm, 53 parts (22 on the bottom side), 46 nets.

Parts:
C1, C2: 4.7uF; C_Rect_L7.0mm_W2.0mm_P5.00mm
C3: 0.33uF; C_Rect_L7.0mm_W2.0mm_P5.00mm
C4: 0.1uF; C_Rect_L7.0mm_W2.0mm_P5.00mm
C5: 1uF; C_Rect_L7.0mm_W2.0mm_P5.00mm
D1: G; LED_D3.0mm
D2, D3, D4, D5: D_Schottky; D_5W_P10.16mm_Horizontal
J1, J2, J14, J15: Conn_01x03_Male; PinHeader_1x03_P2.54mm_Horizontal
J3, J4, J12, J13, J23, J25: Conn_01x04_Male; JST_PH_S4B-PH-K_1x04_P2.00mm_Horizontal
J5, J6, J7: Conn_01x02_Female; BAT-CONN
J8, J10, J20, J21: Conn_01x02_Male; JST_PH_S2B-PH-K_1x02_P2.00mm_Horizontal
J9, J11: Conn_01x02_Male; PinHeader_1x02_P2.54mm_Vertical
J16, J17: Conn_01x06_Male; PinHeader_1x06_P2.54mm_Vertical
J18, J19, J22: Conn_01x03_Male; JST_PH_S3B-PH-K_1x03_P2.00mm_Horizontal
J24: Conn_02x02_Odd_Even; PinHeader_2x02_P2.54mm_Vertical
J26, J27, J28, J30, J31, J32, J33: Conn_01x08_Male; PinHeader_1x08_P2.54mm_Vertical
J29: Conn_02x18_Odd_Even; PinHeader_2x18_P2.54mm_Vertical
L1, L2: 3.3uH; L_Axial_L5.3mm_D2.2mm_P7.62mm_Horizontal_Vishay_IM-1
R1: 330; R_Axial_DIN0204_L3.6mm_D1.6mm_P7.62mm_Horizontal
R2, R3: 4k7; R_Axial_DIN0204_L3.6mm_D1.6mm_P7.62mm_Horizontal
R4: 20k; R_Axial_DIN0204_L3.6mm_D1.6mm_P7.62mm_Horizontal
R5: 12k; R_Axial_DIN0204_L3.6mm_D1.6mm_P7.62mm_Horizontal
U1, U2, U3: L7805; TO-220-3_Vertical

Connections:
/ArduinoMega/5V: C4.1, J3.1, J4.1, J12.1, J13.1, J18.2, J19.2, J22.2, J23.1, J24.2, J25.1, J26.5, R2.2, R3.2, U3.3
/ArduinoMega/8: J30.8, J31.8
/ArduinoMega/9: J30.7, J31.7
/ArduinoMega/10: J30.6, J31.6
/ArduinoMega/11: J30.5, J31.5
/ArduinoMega/12: J30.4, J31.4
/ArduinoMega/13: J30.3, J31.3
/ArduinoMega/A3: C5.1, J27.4, R4.2, R5.1
/ArduinoMega/AREF: J30.1, J31.1
/Connectors/5V-Rpi: D3.2, J24.4, R1.2, U2.3
/Connectors/5V-Servo: D2.2, J1.2, J2.2, J14.2, J15.2, U1.3
A0: J18.3, J27.1
A1: J19.3, J27.2
A2: J22.3, J27.3
BAT+: C1.1, C2.1, C3.1, D4.2, D5.2, J10.1, J11.1, L1.2, L2.2, R4.1, U3.1
CD: J17.4, J29.3
CS: J17.5, J29.4
D0: J20.2, J32.5
D1: J21.2, J32.6
GND: C1.2, C2.2, C3.2, C4.2, C5.2, D1.1, J1.3, J2.3, J3.2, J4.2, J6.1, J7.1, J10.2, J11.2, J12.2, J13.2, J14.3, J15.3, J18.1, J19.1, J20.1, J21.1, J22.1, J23.2, J24.1, J24.3, J25.2, J26.6, J26.7, J29.35, J29.36, J30.2, J31.2, R5.2, U1.2, U2.2, U3.2
MISO: J17.2, J29.31
MOSI: J17.3, J29.32
unnamed: D1.2, R1.1
unnamed: D2.1, L2.1, U1.1
unnamed: D3.1, L1.1, U2.1
unnamed: D4.1, J6.2
unnamed: D5.1, J7.2
unnamed: J5.1, J8.1, J9.1
unnamed: J5.2, J8.2, J9.2
RC1: J16.1, J28.1
RC2: J16.2, J28.2
RC3: J16.3, J28.3
RC4: J16.4, J28.4
RC5: J16.5, J28.5
RC6: J16.6, J28.6
RX_1: J23.4, J33.6
RX_2: J25.4, J33.4
Rudder: J2.1, J32.2
SCK: J17.1, J29.33
SCL: J3.3, J4.3, J12.3, J13.3, J33.8, R3.1
SDA: J3.4, J4.4, J12.4, J13.4, J33.7, R2.1
Sail: J1.1, J32.1
Servo1: J14.1, J32.3
Servo2: J15.1, J32.4
TX_1: J23.3, J33.5
TX_2: J25.3, J33.3

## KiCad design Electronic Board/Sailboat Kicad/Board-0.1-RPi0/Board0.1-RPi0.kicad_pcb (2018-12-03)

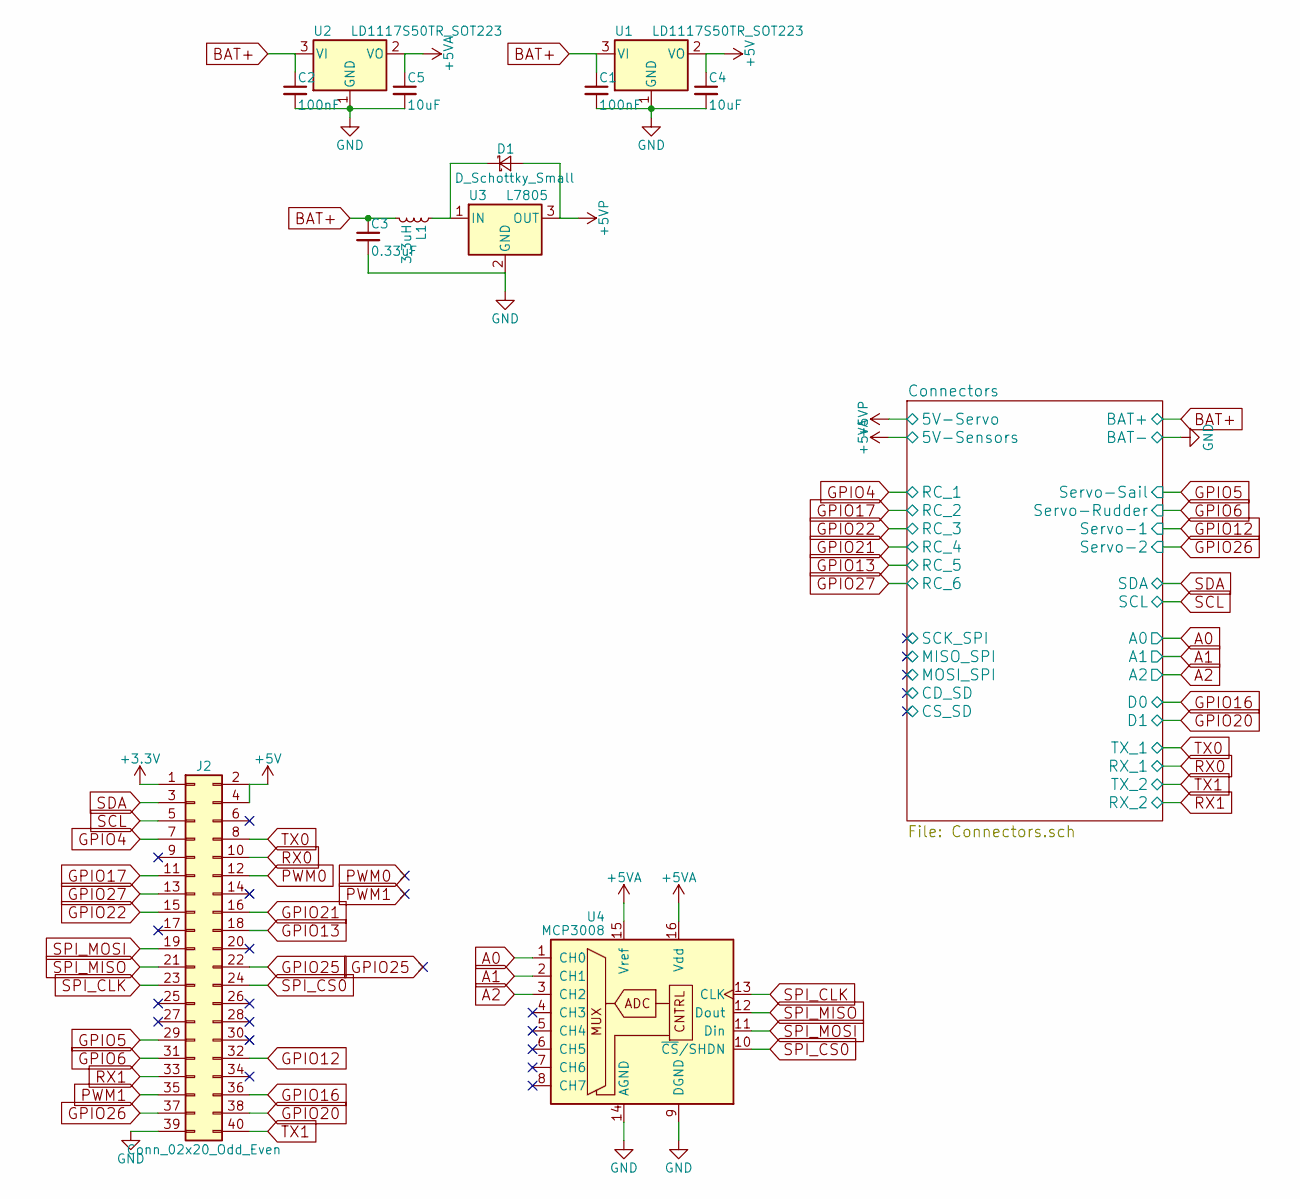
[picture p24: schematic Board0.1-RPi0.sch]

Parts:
C1, C2: 100nF; C_0603
C3: 0.33uF; C_0603
C4, C5: 10uF; C_0603
D1: D_Schottky_Small; D_1206
J2: Conn_02x20_Odd_Even; Pin_Header_Straight_2x20_Pitch2.54mm
L1: 3.3uH; L_0603
U1, U2: LD1117S50TR_SOT223; SOT-223-3_TabPin2
U3: L7805; TO-220-3_Vertical
U4: MCP3008; SOIC-16_3.9x9.9mm_Pitch1.27mm

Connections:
+3V3: J2.1
+5V: C4.1, J2.2, J2.4, U1.2 (VO)
+5VA: C5.1, U2.2 (VO), U4.15 (Vref), U4.16 (Vdd); also elsewhere on the board
+5VP: D1.2 (A), U3.3 (OUT); also elsewhere on the board
A0: U4.1 (CH0); also elsewhere on the board
A1: U4.2 (CH1); also elsewhere on the board
A2: U4.3 (CH2); also elsewhere on the board
BAT+: C1.1, C2.1, C3.1, L1.2, U1.3 (VI), U2.3 (VI); also elsewhere on the board
GND: C1.2, C2.2, C3.2, C4.2, C5.2, J2.39, U1.1 (GND), U2.1 (GND), U3.2 (GND), U4.9 (DGND), U4.14 (AGND); also elsewhere on the board
GPIO4: J2.7; also elsewhere on the board
GPIO5: J2.29; also elsewhere on the board
GPIO6: J2.31; also elsewhere on the board
GPIO12: J2.32; also elsewhere on the board
GPIO13: J2.18; also elsewhere on the board
GPIO16: J2.36; also elsewhere on the board
GPIO17: J2.11; also elsewhere on the board
GPIO20: J2.38; also elsewhere on the board
GPIO21: J2.16; also elsewhere on the board
GPIO22: J2.15; also elsewhere on the board
GPIO25: J2.22
GPIO26: J2.37; also elsewhere on the board
GPIO27: J2.13; also elsewhere on the board
unnamed: D1.1 (K), L1.1, U3.1 (IN)
PWM0: J2.12
PWM1: J2.35
RX0: J2.10; also elsewhere on the board
RX1: J2.33; also elsewhere on the board
SCL: J2.5; also elsewhere on the board
SDA: J2.3; also elsewhere on the board
SPI_CLK: J2.23, U4.13 (CLK)
SPI_CS0: J2.24, U4.10 (~CS~/SHDN)
SPI_MISO: J2.21, U4.12 (Dout)
SPI_MOSI: J2.19, U4.11 (Din)
TX0: J2.8; also elsewhere on the board
TX1: J2.40; also elsewhere on the board

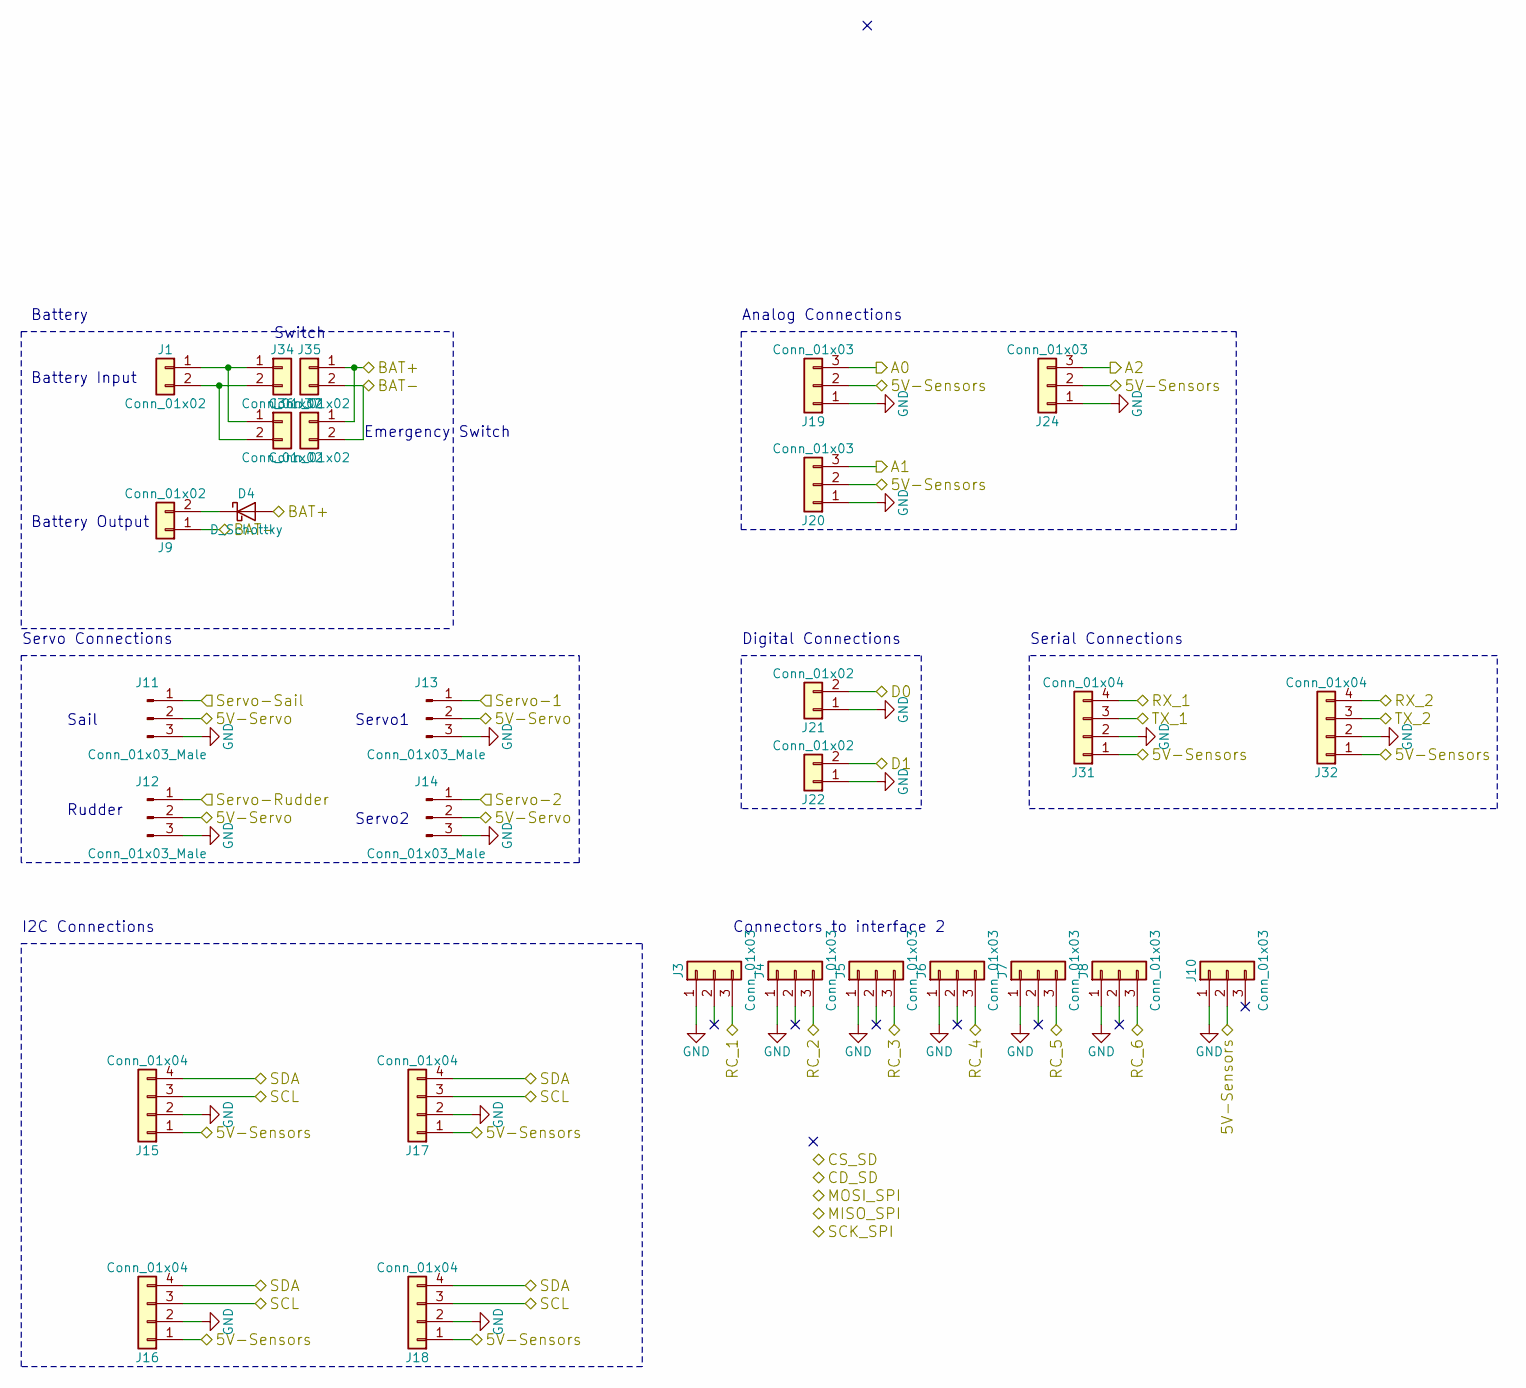
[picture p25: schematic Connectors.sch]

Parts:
D4: D_Schottky; D_5W_P10.16mm_Horizontal
J1, J9: Conn_01x02; BAT-CONN
J3, J4, J5, J6, J7, J8, J10: Conn_01x03; Pin_Header_Straight_1x03_Pitch2.54mm
J11, J12, J13, J14: Conn_01x03_Male; Pin_Header_Angled_1x03_Pitch2.54mm
J15, J16, J17, J18, J31, J32: Conn_01x04; JST_PH_S4B-PH-K_04x2.00mm_Angled
J19, J20, J24: Conn_01x03; JST_PH_S3B-PH-K_03x2.00mm_Angled
J21, J22: Conn_01x02; JST_PH_S2B-PH-K_02x2.00mm_Angled
J34, J35, J36, J37: Conn_01x02; Pin_Header_Straight_1x02_Pitch2.54mm

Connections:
+5VA: J10.2, J15.1, J16.1, J17.1, J18.1, J19.2, J20.2, J24.2, J31.1, J32.1; also elsewhere on the board
+5VP: J11.2, J12.2, J13.2, J14.2; also elsewhere on the board
A0: J19.3; also elsewhere on the board
A1: J20.3; also elsewhere on the board
A2: J24.3; also elsewhere on the board
BAT+: D4.2 (A), J35.1, J37.1; also elsewhere on the board
GND: J3.1, J4.1, J5.1, J6.1, J7.1, J8.1, J9.1, J10.1, J11.3, J12.3, J13.3, J14.3, J15.2, J16.2, J17.2, J18.2, J19.1, J20.1, J21.1, J22.1, J24.1, J31.2, J32.2, J35.2, J37.2; also elsewhere on the board
GPIO4: J3.3; also elsewhere on the board
GPIO5: J11.1; also elsewhere on the board
GPIO6: J12.1; also elsewhere on the board
GPIO12: J13.1; also elsewhere on the board
GPIO13: J7.3; also elsewhere on the board
GPIO16: J21.2; also elsewhere on the board
GPIO17: J4.3; also elsewhere on the board
GPIO20: J22.2; also elsewhere on the board
GPIO21: J6.3; also elsewhere on the board
GPIO22: J5.3; also elsewhere on the board
GPIO26: J14.1; also elsewhere on the board
GPIO27: J8.3; also elsewhere on the board
unnamed: D4.1 (K), J9.2
unnamed: J1.1, J34.1, J36.1
unnamed: J1.2, J34.2, J36.2
RX0: J31.4; also elsewhere on the board
RX1: J32.4; also elsewhere on the board
SCL: J15.3, J16.3, J17.3, J18.3; also elsewhere on the board
SDA: J15.4, J16.4, J17.4, J18.4; also elsewhere on the board
TX0: J31.3; also elsewhere on the board
TX1: J32.3; also elsewhere on the board

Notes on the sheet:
Battery Input
Battery Output
Servo Connections
I2C Connections
Sail
Rudder
Servo1
Servo2
Analog Connections
Battery
Digital Connections
Serial Connections
Switch
Emergency Switch
Connectors to interface 2

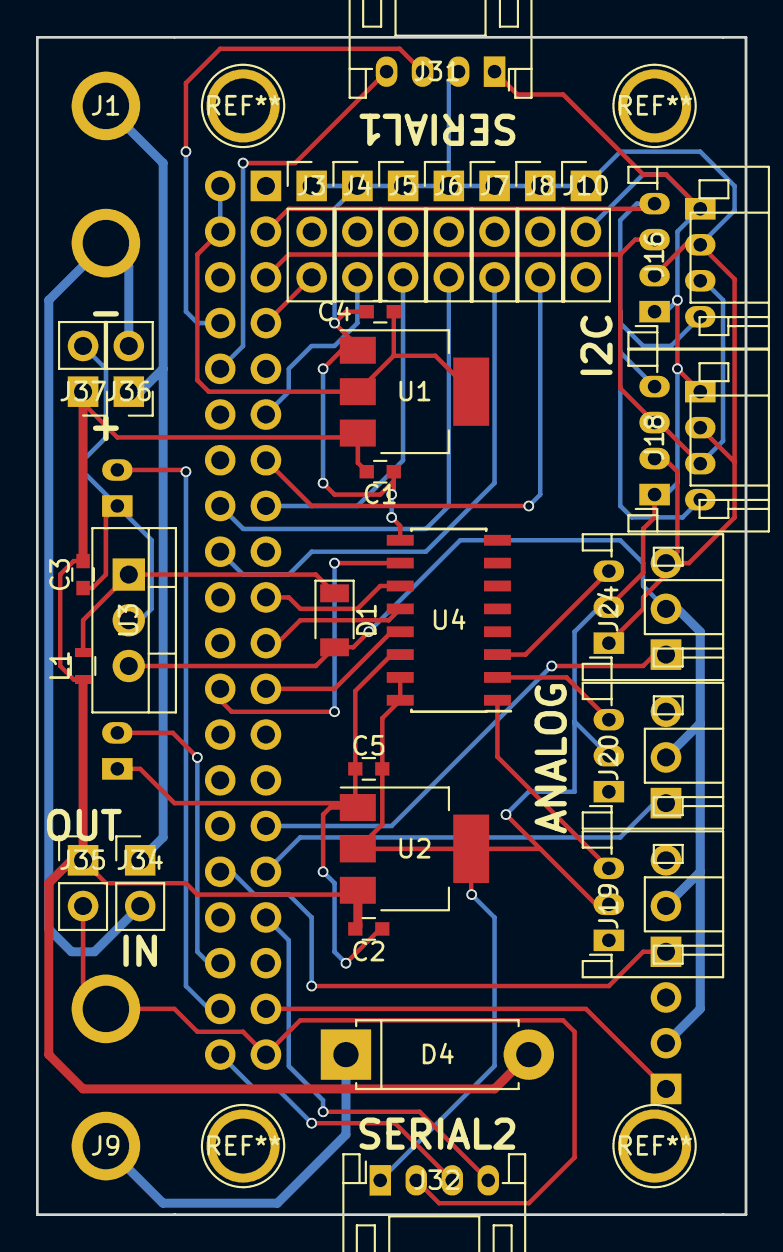
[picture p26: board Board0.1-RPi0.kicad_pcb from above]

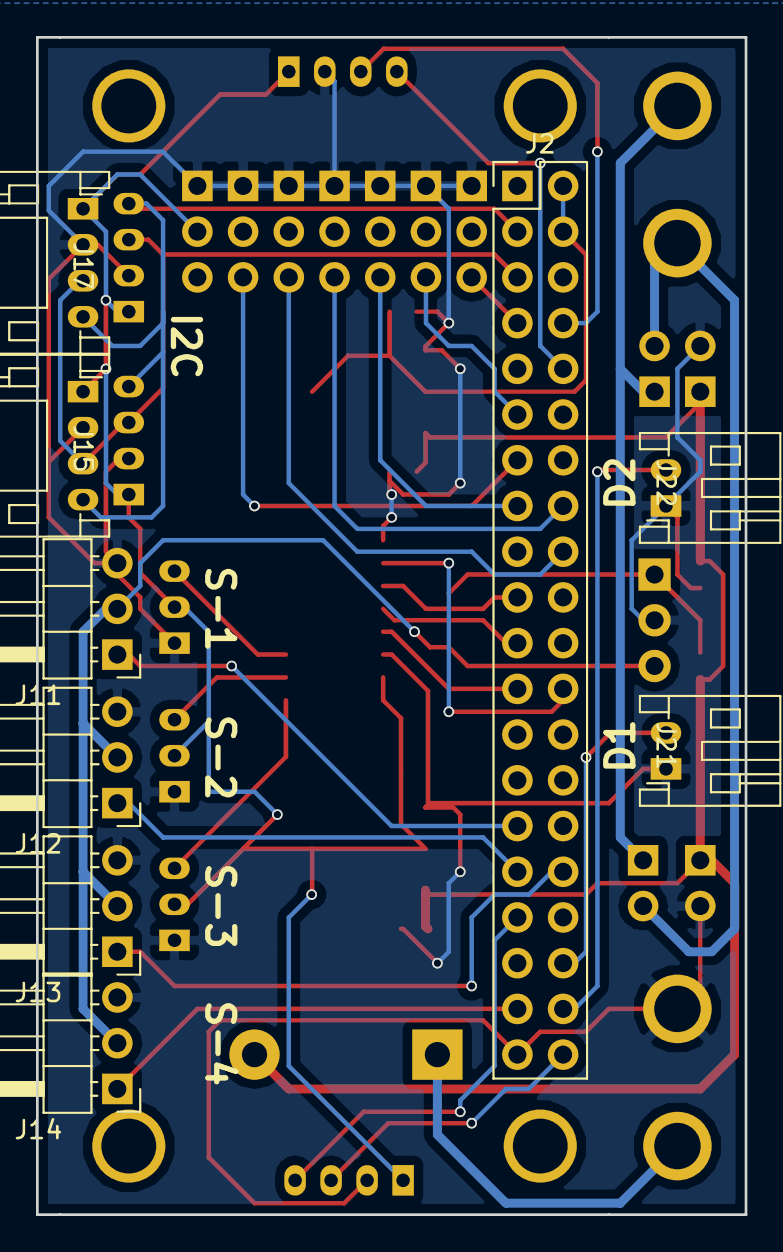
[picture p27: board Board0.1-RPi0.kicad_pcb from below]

Board: 2 copper layers, 39.4 x 65.4 mm, 41 parts (9 on the bottom side), 34 nets.

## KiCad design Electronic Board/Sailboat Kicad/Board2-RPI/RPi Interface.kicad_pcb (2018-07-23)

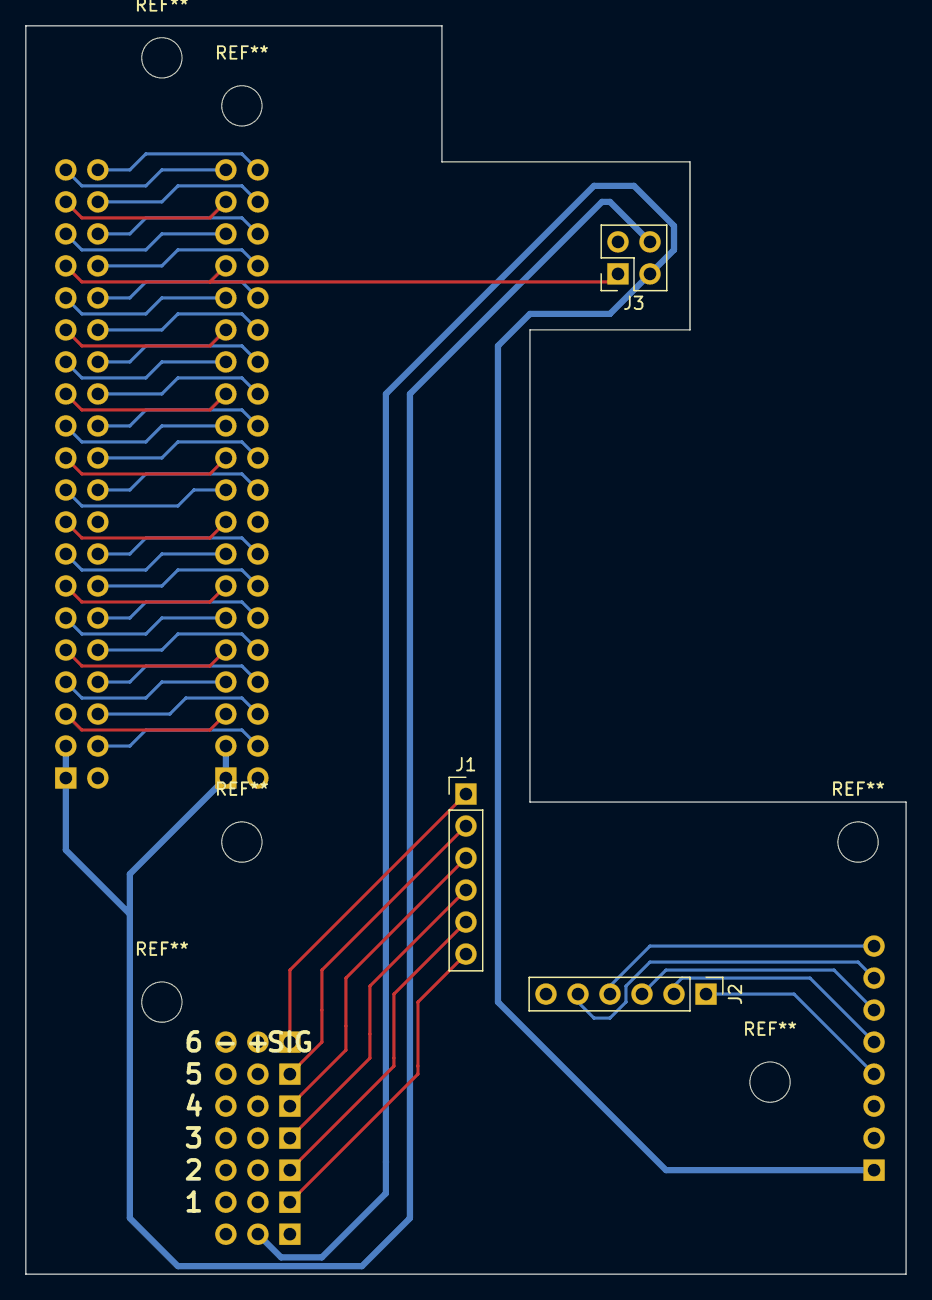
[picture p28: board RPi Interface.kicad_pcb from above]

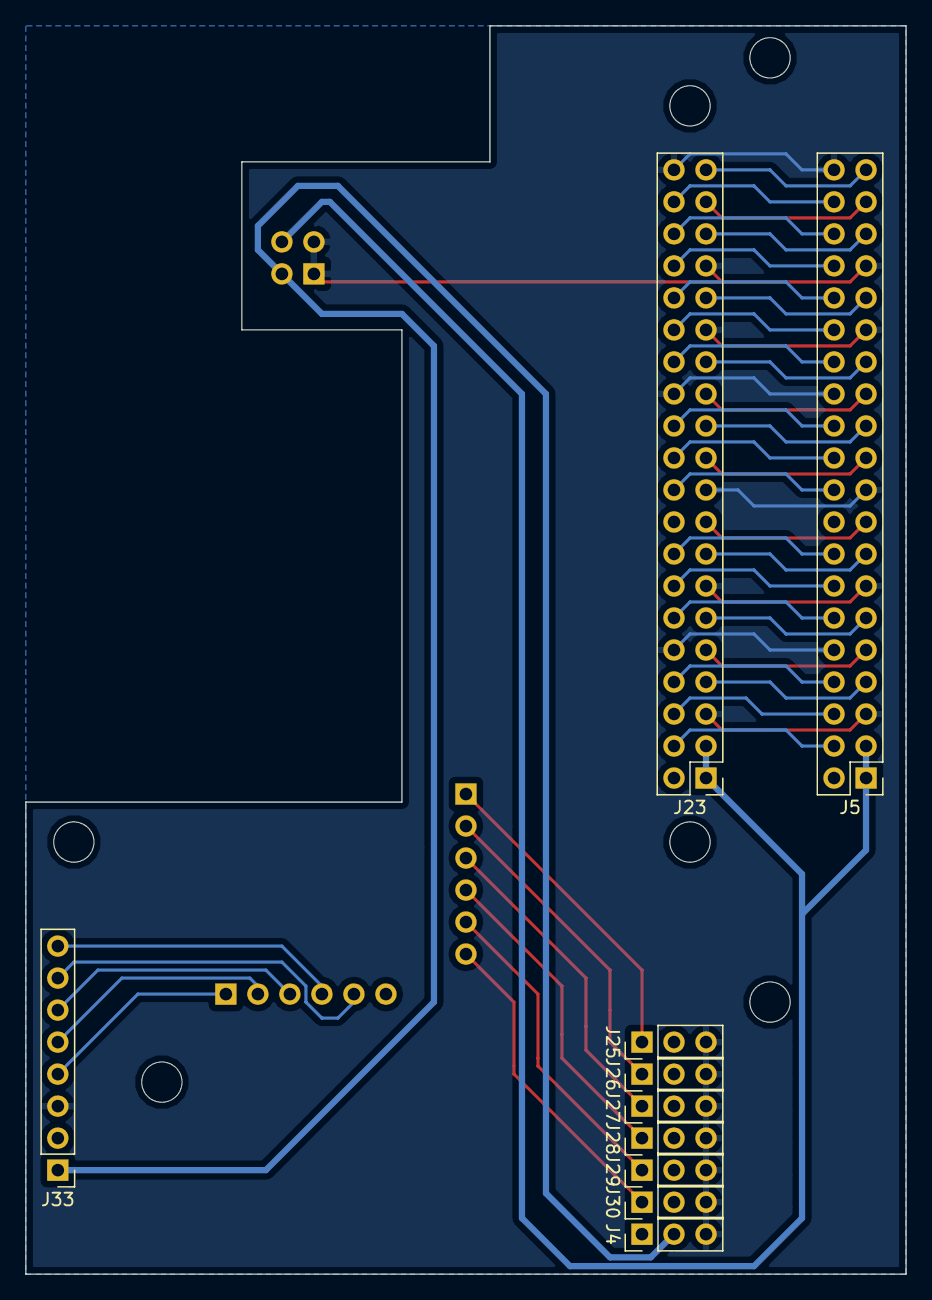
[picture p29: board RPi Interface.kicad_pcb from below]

Board: 2 copper layers, 69.9 x 99.1 mm, 13 parts (10 on the bottom side), 42 nets.

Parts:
J1, J2: Conn_01x06; Socket_Strip_Straight_1x06_Pitch2.54mm
J3: Conn_02x02_Odd_Even; Socket_Strip_Straight_2x02_Pitch2.54mm
J4, J25, J26, J27, J28, J29, J30: Conn_01x03_Female; Socket_Strip_Straight_1x03_Pitch2.54mm
J5, J23: Conn_02x20_Odd_Even; Pin_Header_Straight_2x20_Pitch2.54mm
J33: Conn_01x08_Female; Socket_Strip_Straight_1x08_Pitch2.54mm

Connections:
5V-Sensors: J3.2, J4.2, J33.1
/Connectors/5V-RPi: J3.4, J5.1, J5.3, J23.1, J23.3
/RPi/2_RPi: J5.4, J23.4
/RPi/3_RPi: J5.6, J23.6
/RPi/4_RPi: J5.8, J23.8
/RPi/5_RPi: J5.30, J23.30
/RPi/6_RPi: J5.32, J23.32
/RPi/7_RPi: J5.25, J23.25
/RPi/8_RPi: J5.23, J23.23
/RPi/9_RPi: J5.22, J23.22
/RPi/10_RPi: J5.20, J23.20
/RPi/11_RPi: J5.24, J23.24
/RPi/12_RPi: J5.31, J23.31
/RPi/13_RPi: J5.34, J23.34
/RPi/14_RPi: J5.7, J23.7
/RPi/15_RPi: J5.9, J23.9
/RPi/16_RPi: J5.35, J23.35
/RPi/17_RPi: J5.12, J23.12
/RPi/18_RPi: J5.11, J23.11
/RPi/19_RPi: J5.36, J23.36
/RPi/20_RPi: J5.37, J23.37
/RPi/21_RPi: J5.39, J23.39
/RPi/22_RPi: J5.16, J23.16
/RPi/23_RPi: J5.15, J23.15
/RPi/24_RPi: J5.17, J23.17
/RPi/25_RPi: J5.21, J23.21
/RPi/26_RPi: J5.38, J23.38
/RPi/27_RPi: J5.14, J23.14
/RPi/ID_SC: J5.27, J23.27
/RPi/ID_SD: J5.28, J23.28
CD_SD: J2.4, J33.8
CS_SD: J2.5, J33.7
GND: J3.1, J3.3, J4.3, J5.5, J5.10, J5.13, J5.19, J5.26, J5.29, J5.33, J5.40, J23.5, J23.10, J23.13, J23.19, J23.26, J23.29, J23.33, J23.40, J25.3, J26.3, J27.3, J28.3, J29.3, J30.3, J33.3
MISO_SPI: J2.2, J33.5
MOSI_SPI: J2.3, J33.6
RC_1: J1.1, J25.1
RC_2: J1.2, J26.1
RC_3: J1.3, J27.1
RC_4: J1.4, J28.1
RC_5: J1.5, J29.1
RC_6: J1.6, J30.1
SCK_SPI: J2.1, J33.4

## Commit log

2018-03-22 Separated Boards for smaller factor
    [AHRS.sch, ATMega.sch, Arduino Interface.kicad_pcb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]
2018-03-23 Finished board-v0.1
    [Arduino Interface.kicad_pcb, Arduino Interface.sch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]
2018-03-26 Finished 2 boards and submitted for manufacturing
    [Arduino Interface.kicad_pcb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]
2018-03-28 BOM of the boat
    [BOM.xlsx]
2018-03-28 Updated wrong sources to BOM
    [BOM.xlsx]
2018-04-03 3D and png of final boards
    [RPiInt.stl]
2018-04-19 Added GPS Box 3Ds
    [GPS.SLDASM, GPSBot.SLDPRT, GPSBot.STL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]
2018-04-19 Hotfix on raspberry pi Card Radio interface
    [RPi Interface.kicad_pcb]
2018-04-19 Hotfix again for Radio on Rasbperry pi
    [RPi Interface.kicad_pcb]
2018-04-20 Hotfix GPS Box for waterproofing and screws. Xsens box added
    [GPS.SLDASM, GPSBot.SLDPRT, GPSBot.STL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]
2018-05-29 Cleaned up, and added security, text and better usability, preparation for board v2
    [Arduino Interface.kicad_pcb, Arduino Interface.sch, ArduinoInt.FCStd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]
2018-05-29 Prepared gerber and pdf files
    [Arduino Interface-B.Cu.gbl, Arduino Interface-B.Mask.gbs, Arduino Interface-B.SilkS.gbo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]
2018-06-01 Minor changes and recompiled gerber, pdf and 3D
    [Arduino Interface-B.Cu.gbl, Arduino Interface-B.Cu.gbr, Arduino Interface-B.Mask.gbr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]
2018-06-01 Changed size to be smaller than 100mm
    [Arduino Interface-B.Cu.gbl, Arduino Interface-B.Cu.gbr, Arduino Interface-B.Mask.gbr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]
2018-06-04 Updated BOM for new board and wrong products
    [BOM.xlsx]
2018-07-23 New board bug fix
    [Arduino Interface-B.Cu.gbl, Arduino Interface-B.Mask.gbs, Arduino Interface-B.SilkS.gbo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]
2018-09-13 added decoupler capacitor for voltage measurements and added connectors to arduino
    [Arduino Interface-B.Cu.gbl, Arduino Interface-B.Mask.gbs, Arduino Interface-B.SilkS.gbo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]
2018-09-13 Beginning a small control box with raspberry pi zero and naked mega 4
    [Board0.1-RPi0.kicad_pcb, Board0.1-RPi0.sch]
2018-09-13 Removed the arduino. Why keep it?? Doesn't make sense :/
    [Board0.1-RPi0.kicad_pcb, Board0.1-RPi0.sch]
2018-09-14 Components installed for a working rpi0 shield for sailboat
    [Board0.1-RPi0.kicad_pcb, Board0.1-RPi0.sch, Connectors.sch]
2018-09-14 Finished tracing the RPi0 Board and plotted the gerbers, ready for production
    [Board0.1-RPi0.kicad_pcb, Board0.1-RPi0.sch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]
2018-12-03 Began RPI0 board
    [Board0.1-RPi0.kicad_pcb, Board0.1-RPi0.sch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]
2019-06-11 Updated version of Kicad, rendered images and BOM
    [Arduino Interface.kicad_pcb, Arduino Interface.sch, ArduinoMega.sch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]
2019-06-11 Added BOM of the RPI
    [BOM.xlsx]
2019-06-11 Upgrade Kicad Version and PDF Schematics
    [Connectors-2019-06-11-16-40-35.sch, RPi Interface-2019-06-11-16-40-35.sch, RPi-2019-06-11-16-40-35.sch]
